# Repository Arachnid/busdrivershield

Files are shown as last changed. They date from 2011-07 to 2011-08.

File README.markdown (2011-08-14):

BusDriver Shield
===============

The BusDriver Shield is a stackable Arduino shield for driving low-power DC or
stepper motors over I2C.

Features:

 - 100% stackable. The number of stacked shields you can drive is limited only
   by the available current on the vin (motor) and 5v rails, and the number of
   I2C addresses available.
 - PWM control for variable speed control.
 - Each board can drive two 1A motors, or the outputs can be combined to drive
   one higher current motor.
 - Optional kickback diodes protect the H-Bridge from inductive kickback.
 - Can be configured to use any valid I2C address in software.
 - Screw terminals for two inputs per motor support a pair of limit switches or
   quadrature encoder per motor. Set-and-forget operation takes the strain of
   handling encoder input off the Arduino.
 - Events can be signalled back to the host board on interrupt pins 2 or 3,
   software-selectable.

Hardware
--------

The BusDriver Shield has two main components: An ATTiny2313 MCU, and an SN754410
quad half H-Bridge. The MCU takes care of the logic and communicates over the
I2C bus, while the H-Bridge takes care of motor driving. Optional kickback
diodes provide additional protection against inductive kickback; also included
are optional power smoothing capacitors and I2C pullups.

Pin assignments for the MCU are as follows:

 - OC1A and OC1B connect to the H-Bridge's enable lines,
   permitting PWM control of each motor.
 - PB0-PB2 and PB6 connect to the input sensors for limit switches or quadrature
   encoders. Pin change interrupts on these lines allow effective handling of
   encoder events.
 - PD2-PD5 connect to the direction control lines on each H-Bridge.
 - PD1 and PD6 connect to Arduino pins 2 and 3 for signalling interrupts to the
   host processor.
 - SCL and SDA connect to the Arduino's A4 and A5 pins for I2C communication
   with the host Arduino.

Software
--------

The ATTiny2313 MCU on each shield exposes an I2C based control interface. All
functionality is exposed via a set of 8-bit registers which can be read and
written over I2C.

To read a register, write a single byte to the device - the register number -
then read a single byte, which will be the contents of the register.

To write a register, write two bytes to the device - the register number and its
value, respectively.

By default, register changes are not persistent, and the device will reset to
its default state if power is removed and restored. Register changes can be 
made permanent by writing to register 255, STORE.

Register mappings are described below.

### Register 0: ADDR

<table>
  <tr><th>7</th><th>6</th><th>5</th><th>4</th><th>3</th><th>2</th><th>1</th><th>0</th></tr>
  <tr><td colspan="8">ADDRESS</td></tr>
</table>

The ADDR register stores the I2C address of the shield as an 8-bit unsigned
integer. Writing to this register will change the shield's address for all future
communications.

### Register 1: STATUS

<table>
  <tr><th>7</th><th>6</th><th>5</th><th>4</th><th>3</th><th>2</th><th>1</th><th>0</th></tr>
  <tr><td colspan="2">Reserved</td><td>INT1</td><td>INT0</td><td>M2_I2</td><td>M2_I1</td><td>M1_I2</td><td>M1_I1</td></tr>
</table>

The STATUS register contains general device status information. The INT0 and
INT1 bits reflect the current status of the two interrupt pins. Writing a 0 to
them will clear the interrupt, while writing a 1 has no effect. The Mx_Iy bits
reflect the current status of input y on motor x. If the relevant
INOPT[x].INVERT_Iy bit is set, the value here will be the inverse of the state
of the actual pin.

### Register 2: DIR

<table>
  <tr><th>7</th><th>6</th><th>5</th><th>4</th><th>3</th><th>2</th><th>1</th><th>0</th></tr>
  <tr><td colspan="4">Reserved</td><td colspan="2">M2</td><td colspan="2">M1</td></tr>
</table>

The DIR register controls the direction of motion for each motor. For each,
values of 00 and 11 indicate no movement - active braking if the motor is
engaged - while 01 and 10 indicate clockwise and counterclockwise motion,
respectively (how this translates into motion on your motor will depend on how
it is wired up).

One special case to note is that if limit switch behaviour is enabled with
INOPT[x].LIMIT_Iy, the limit switch being triggered will set the corresponding
bit of the direction register to 0. If the register was set to 11, this could
cause the motor to start moving. If this behaviour is not desired, set the
register to 00 when no motion is desired.

### Register 3: Reserved

This register is reserved for future use. All reads return 0, and writes will be
ignored.

### Registers 4 & 5: SPEED

<table>
  <tr><th>7</th><th>6</th><th>5</th><th>4</th><th>3</th><th>2</th><th>1</th><th>0</th></tr>
  <tr><td colspan="8">SPEED</td></tr>
</table>

The two speed registers control the speed of each motor. SPEED[0] controls motor
1, while SPEED[1] controls motor 2. Each register is treated as a single 8-bit
unsigned integer. Setting the value to 0 holds the enable pin of the H-Bridge
port for the relevant motor low, while setting it to 255 holds it high.
Intermediate values cause a PWM waveform to be output with a corresponding
duty-cycle.

### Registers 6 & 7: INOPTS

<table>
  <tr><th>7</th><th>6</th><th>5</th><th>4</th><th>3</th><th>2</th><th>1</th><th>0</th></tr>
  <tr><td colspan="2">Reserved</td><td>LIMIT_I2</td><td>LIMIT_I1</td><td>INVERT_I2</td><td>INVERT_I1</td><td>PULLUP_I2</td><td>PULLUP_I1</td></tr>
</table>

The two inopts registers control input options for each motor. INOPTS[0]
controls settings for the first motor, while INOPTS[1] controls settings for the
second one.

LIMIT_I1 and LIMIT_I2 control limit behaviour. If the LIMIT_In bit is set, and
the correspondingly numbered input becomes high (after being inverted, if
specified by INVERT_In), the relevant bit in the direction register will be set
to 0, halting the motor if it was moving. Thus, limit switches can be connected
to the relevant inputs to cause the motor to halt when it reaches a limit. Note
that while the direction bit will be unset, the speed register will be left
unmodified.

INVERT_I1 and INVERT_I2 control how inputs are treated. If the INVERT_In bit is
set, the correspondingly numbered input has its value inverted. This inverted
value is used in all locations, including when considering limit behaviour and
in the STATUS register.

PULLUP_I1 and PULLUP_I2 control the pullups on each input pin. If the relevant
bit is set, pullups will be enabled for that input pin.

### Registers 8 & 9: IMASK

<table>
  <tr><th>7</th><th>6</th><th>5</th><th>4</th><th>3</th><th>2</th><th>1</th><th>0</th></tr>
  <tr><td colspan="4">Reserved</td><td>LIMIT_M2_I2</td><td>LIMIT_M2_I1</td><td>LIMIT_M1_I2</td><td>LIMIT_M1_I1</td></tr>
</table>

The two imask registers control the conditions under which an interrupt will be
triggered. Triggering an interrupt results in setting the relevant bit in the
STATUS register, and pulling the relevant input pin LOW.

When an interrupt is not being triggered, the pin is left in a high-impedance
state. This convention is present for two reasons: By pulling the pin low,
rather than high, pullups can be used by the Arduino to make the pin normally
high. By setting the normal state to high impedance, multiple motor shields can
use the same interrupt line, and if the interrupt is not required, the pin can
be used for other purposes.

Each of the LIMIT_Ma_Ib bits controls whether the input will be triggered when
the corresponding input pin becomes high (after inversion if INOPTS[a].INVERT_Ib
is set).

### Register 127: STORE

Normally, changes made to registers persist only until power is removed. On each
startup, default values for each register are read from the processor's EEPROM.

Writing any value to the STORE register causes the current state of all
registers to be asynchronously written to permanent EEPROM storage. On
subsequent boots, the stored values will be loaded and used as defaults.

Default values, when loaded, are treated the same as if they had been set using
standard I2C commands. As a result, regardless of the value of the STATUS
register when STORE was written to, it will always be initialized with all bits
unset. All other registers, including the speed and direction registers, will
be initialized to the values they had when the write occurred.

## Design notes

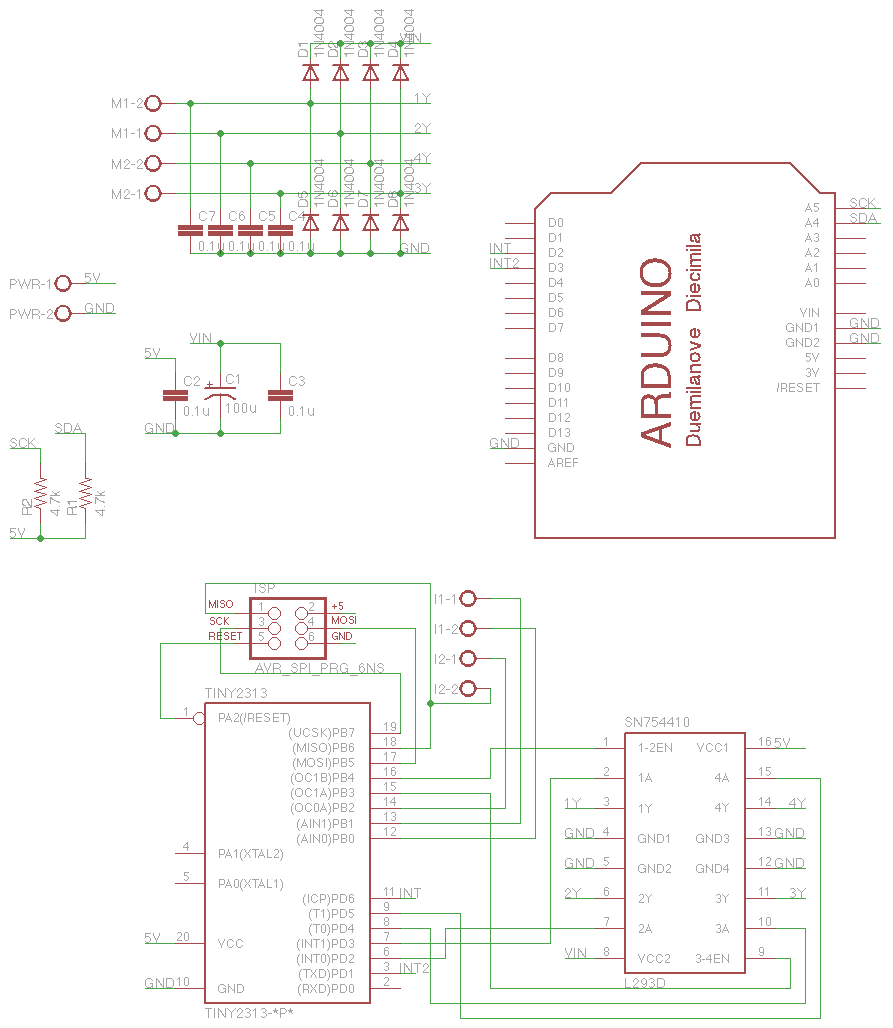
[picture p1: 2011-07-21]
schematics/shield_schematic.png

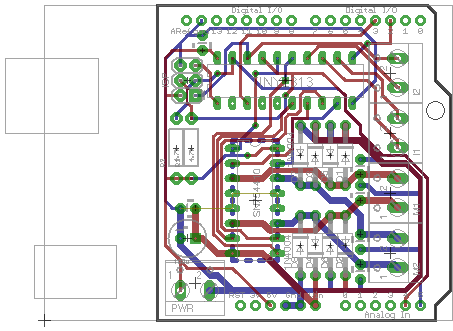
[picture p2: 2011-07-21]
schematics/shield_pcb.png

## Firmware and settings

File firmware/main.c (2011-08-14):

/*
 * BusDriver shield - an I2C based motor driver shield for Arduino.
 * Copyright (C) 2011 Nick Johnson
 *
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
 * You should have received a copy of the GNU General Public License
 * along with this program; if not, write to the Free Software
 * Foundation, Inc., 51 Franklin Street, Fifth Floor, Boston, MA  02110-1301, USA.
 */

#define F_CPU 1000000UL  // 1 MHz

#include <util/delay.h>
#include <avr/io.h>
#include <avr/eeprom.h>
#include <avr/interrupt.h>
#include <avr/pgmspace.h>
#include "register.h"
#include "usiTwiSlave.h"

#define TRUE 1
#define FALSE 0

#define copy_bit(from_reg, from_bit, to_reg, to_bit) if((from_reg) & _BV(from_bit)) { \
    to_reg |= _BV(to_bit); \
} else { \
    to_reg &= ~_BV(to_bit); \
}

#define DDR_ENABLE DDRB
#define DD_ENABLE1 DDB4
#define DD_ENABLE2 DDB3
#define ENABLE_PWM_SETUP() TCCR1A = _BV(WGM10), TCCR1B = _BV(WGM12) | _BV(CS10)
#define TCCR_ENABLE TCCR1A
#define COM_ENABLE1 _BV(COM1B1)
#define COM_ENABLE2 _BV(COM1A1)
#define OCR_ENABLE1 OCR1B
#define OCR_ENABLE2 OCR1A

#define PORT_INPUT PORTB
#define PIN_INPUT PINB
#define P_INPUT_M1_I1 PB6
#define P_INPUT_M1_I2 PB2
#define P_INPUT_M2_I1 PB0
#define P_INPUT_M2_I2 PB1
#define PCINT_MASK _BV(PCINT0) | _BV(PCINT1) | _BV(PCINT2) | _BV(PCINT6)

#define PORT_DIR PORTD
#define P_DIR_M1_CCW PD3
#define P_DIR_M1_CW PD2
#define P_DIR_M2_CCW PD5
#define P_DIR_M2_CW PD4
#define DDR_DIR DDRD
#define DD_DIR1 DDD3
#define DD_DIR2 DDD2
#define DD_DIR3 DDD5
#define DD_DIR4 DDD4

#define PORT_INT PORTD
#define DDR_INT DDRD
#define DD_INT0 DDD6
#define P_INT0 PD6
#define DD_INT1 DDD1
#define P_INT1 PD1

typedef void (*register_write_handler)(uint8_t reg, uint8_t *value);

// Predefinitions of read/write handlers so we can reference them
uint8_t i2c_read(uint8_t reg);
void i2c_write(uint8_t reg, uint8_t value);
void main(void) __attribute__((noreturn));

register_t registers;
// EEPROM copy of registers; updated on write to register 255.
register_t EEMEM eeprom_registers = {
    .reg = {
        .slave_addr = 0x26,
        .status = 0,
        .direction = 0,
        .reserved = 0,
        .speed = {0, 0},
        .inopts = {0, 0},
        .int_mask = {0, 0},
    }
};

volatile uint8_t eeprom_dirty = FALSE;

void write_slave_addr(uint8_t reg, uint8_t *value) {
    usiTwiSlaveInit(*value, i2c_read, i2c_write);
}

void write_status(uint8_t reg, uint8_t *value) {
    // Clear interrupt pins if requested
    if(!(_BV(STATUS_INT0) & *value))
        DDR_INT &= ~_BV(DD_INT0);
    if(!(_BV(STATUS_INT1) & *value))
        DDR_INT &= ~_BV(DD_INT1);
    
    // No writing to input bits, and interrupt bits can only be cleared
    int value_mask = *value | ~(_BV(STATUS_INT0) | _BV(STATUS_INT1));
    *value = value_mask & registers.reg.status;
}

void write_direction(uint8_t reg, uint8_t *value) {
    // Mask out unused bits
    *value &= _BV(DIR_M1_CCW) | _BV(DIR_M1_CW) |
              _BV(DIR_M2_CCW) | _BV(DIR_M2_CW);

    // Unset any bits prohibited by limit switches
    if((registers.reg.status | _BV(STATUS_M1_I1)) &&
       (registers.reg.inopts[0] | _BV(INOPT_LIMIT_I1)))
        *value &= ~_BV(DIR_M1_CCW);
    if((registers.reg.status | _BV(STATUS_M1_I2)) &&
       (registers.reg.inopts[0] | _BV(INOPT_LIMIT_I2)))
        *value &= ~_BV(DIR_M1_CW);
    if((registers.reg.status | _BV(STATUS_M2_I1)) &&
       (registers.reg.inopts[1] | _BV(INOPT_LIMIT_I1)))
        *value &= ~_BV(DIR_M2_CCW);
    if((registers.reg.status | _BV(STATUS_M2_I2)) &&
       (registers.reg.inopts[1] | _BV(INOPT_LIMIT_I2)))
        *value &= ~_BV(DIR_M2_CW);
    
    // Set outputs as required
    copy_bit(*value, DIR_M1_CCW, PORT_DIR, P_DIR_M1_CCW);
    copy_bit(*value, DIR_M1_CW, PORT_DIR, P_DIR_M1_CW);
    copy_bit(*value, DIR_M2_CCW, PORT_DIR, P_DIR_M2_CCW);
    copy_bit(*value, DIR_M2_CW, PORT_DIR, P_DIR_M2_CW);
}

void write_reserved(uint8_t reg, uint8_t *value) {
    //*value = 0;
}

void write_speed(uint8_t reg, uint8_t *value) {
    uint8_t tccr; // TCCR register bitmask to activate the specified motor
    volatile uint16_t *ocr; // Register to set PWM duty cycle for specified motor

    if((reg & 1) == 0) {
        // Motor 1
        tccr = COM_ENABLE1;
        ocr = &OCR_ENABLE1;
    } else {
        // Motor 2
        tccr = COM_ENABLE2;
        ocr = &OCR_ENABLE2;
    }

    if(*value == 0) {
        // Disable PWM for constant 0
        TCCR_ENABLE &= ~tccr;
    } else {
        // Enable PWM and set duty cycle
        TCCR_ENABLE |= tccr;
        *ocr = *value;
    }
}

void write_inopts(uint8_t reg, uint8_t *value) {
    if(reg & 1) {
        copy_bit(*value, INOPT_PULLUP_I1, PORT_INPUT, P_INPUT_M2_I1);
        copy_bit(*value, INOPT_PULLUP_I2, PORT_INPUT, P_INPUT_M2_I2);
    } else {
        copy_bit(*value, INOPT_PULLUP_I1, PORT_INPUT, P_INPUT_M1_I1);
        copy_bit(*value, INOPT_PULLUP_I2, PORT_INPUT, P_INPUT_M1_I2);
    }
    
    // Update input pin status, limits etc
    update_inputs();
}

void write_int_mask(uint8_t reg, uint8_t *value) {
}

const register_write_handler write_handlers[] = {
    write_slave_addr,
    write_status,
    write_direction,
    write_reserved,
    write_speed,
    write_speed,
    write_inopts,
    write_inopts,
    write_int_mask,
    write_int_mask,
};

uint8_t i2c_read(uint8_t reg) {
    if(reg < NUM_REGISTERS) {
        return registers.bytes[reg];
    } else {
        return 0;
    }
}

void i2c_write(uint8_t reg, uint8_t value) {
    if(reg < NUM_REGISTERS) {
        write_handlers[reg](reg, &value);
        registers.bytes[reg] = value;
    } else if(reg == 127) {
        // Update eeprom (asynchronously, so we don't block the interrupt).
        eeprom_dirty = TRUE;
    } else {
        // Invalid register - do nothing.
    }
}

void update_input_pin(uint8_t pin, uint8_t input_id) {
    // This function makes the following assumptions:
    // 1) There are exactly 4 inputs
    // 2) The bit position for each input is the same in the STATUS and IMASK registers
    // 3) Bit 1 of input_id can be used to choose which inopts register to select
    // 4) Bit 0 of input_id can be used to choose which offset into the inopts
    //    register to use for the invert and limit bits.
    // 5) The bit position for each input matches the bit in the direction register
    //    it should clear if limit behaviour is configured.
    
    // Get the contents of the inopts register for this input (assumption 3)
    uint8_t inopts = registers.reg.inopts[input_id >> 1];

    // Get the pin value
    uint8_t val = PIN_INPUT & _BV(pin);

    // If the invert flag is set, invert the input (assumption 4)
    if(inopts & _BV(INOPT_INVERT_I1 + (input_id & 1))) {
        val = !val;
    }
    
    // Update the status register (assumption 2)
    if(val) {
        registers.reg.status |= _BV(input_id);
    } else {
        registers.reg.status &= ~_BV(input_id);
    }
    
    // Stop the motor if limits are set (assumptions 4 & 5)
    if(val && (inopts & _BV(INOPT_LIMIT_I1 + (input_id & 1)))) {
        if(registers.reg.direction & _BV(input_id)) {
            registers.reg.direction &= ~_BV(input_id);
            write_direction(2, &registers.reg.direction);
        }
    }
    
    // Signal an interrupt if requested
    if(registers.reg.int_mask[0] & _BV(input_id)) {
        registers.reg.status |= _BV(STATUS_INT0);
        DDR_INT |= _BV(DD_INT0);
    }
    if(registers.reg.int_mask[1] & _BV(input_id)) {
        registers.reg.status |= _BV(STATUS_INT1);
        DDR_INT |= _BV(DD_INT1);
    }
}

void update_inputs() {
    update_input_pin(P_INPUT_M1_I1, 0);
    update_input_pin(P_INPUT_M1_I2, 1);
    update_input_pin(P_INPUT_M2_I1, 2);
    update_input_pin(P_INPUT_M2_I2, 3);
}   

ISR(PCINT_vect) {
    // One of the input pins has changed value.
    update_inputs();
}

void ioinit(void) {
    // Set the enable pins as outputs
    DDR_ENABLE |= _BV(DD_ENABLE1) | _BV(DD_ENABLE2);
    // Setup PWM: Fast PWM mode, 8-bit, no prescaling. Don't enable it yet.
    ENABLE_PWM_SETUP();
    // Set the direction pins as outputs
    DDR_DIR |= _BV(DD_DIR1) | _BV(DD_DIR2) | _BV(DD_DIR3) | _BV(DD_DIR4);
}

void configure_interrupts(void) {
    // Enable the pin change interrupt for the relevant pins
    PCMSK |= PCINT_MASK;
    // Turn on the pin change interrupt globally
    GIMSK |= _BV(PCIE);
}

void read_registers(void) {
    // Initialize from eeprom
    eeprom_read_block(&registers, &eeprom_registers, sizeof(registers));

    // Run all the write funcs in order to initialize the device
    for(int i = 0; i < NUM_REGISTERS; i++)
        write_handlers[i](i, &registers.bytes[i]);
}

void main(void) {
    ioinit();
    configure_interrupts();
    read_registers();
    // Enable interrupts
    sei();
    
    for(;;) {
        if(eeprom_dirty) {
            eeprom_write_block(&registers, &eeprom_registers, sizeof(registers));
            eeprom_dirty = FALSE;
        }
    }
}

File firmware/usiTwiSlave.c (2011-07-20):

/********************************************************************************

USI TWI Slave driver.

Created by Donald R. Blake. donblake at worldnet.att.net
Adapted by Jochen Toppe, jochen.toppe at jtoee.com
Adapted by Ben Galvin, bgalvin at fastmail.fm

---------------------------------------------------------------------------------

Created from Atmel source files for Application Note AVR312: Using the USI Module
as an I2C slave.

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
---------------------------------------------------------------------------------

Change Activity:

    Date       Description
   ------      -------------
  16 Mar 2007  Created.
  27 Mar 2007  Added support for ATtiny261, 461 and 861.
  26 Apr 2007  Fixed ACK of slave address on a read.
  04 Jul 2007  Fixed USISIF in ATtiny45 def
  12 Dev 2009  Added callback functions for data requests
  12 Apr 2011  Added read/write register callbacks
********************************************************************************/



/********************************************************************************

                                    includes

********************************************************************************/

#include <avr/io.h>
#include <avr/interrupt.h>
#include <stdbool.h>
#include "usiTwiSlave.h"



/********************************************************************************

                            device dependent defines

********************************************************************************/

#if defined( __AVR_ATtiny2313__ )
#  define DDR_USI             DDRB
#  define PORT_USI            PORTB
#  define PIN_USI             PINB
#  define PORT_USI_SDA        PB5
#  define PORT_USI_SCL        PB7
#  define PIN_USI_SDA         PINB5
#  define PIN_USI_SCL         PINB7
#  define USI_START_COND_INT  USISIF
#  define USI_START_VECTOR    USI_START_vect
#  define USI_OVERFLOW_VECTOR USI_OVERFLOW_vect
#endif

#if defined( __AVR_ATtiny25__ ) | \
     defined( __AVR_ATtiny45__ ) | \
     defined( __AVR_ATtiny85__ )
#  define DDR_USI             DDRB
#  define PORT_USI            PORTB
#  define PIN_USI             PINB
#  define PORT_USI_SDA        PB0
#  define PORT_USI_SCL        PB2
#  define PIN_USI_SDA         PINB0
#  define PIN_USI_SCL         PINB2
#  define USI_START_COND_INT  USISIF
#  define USI_START_VECTOR    USI_START_vect
#  define USI_OVERFLOW_VECTOR USI_OVF_vect
#endif

#if defined( __AVR_ATtiny26__ )
#  define DDR_USI             DDRB
#  define PORT_USI            PORTB
#  define PIN_USI             PINB
#  define PORT_USI_SDA        PB0
#  define PORT_USI_SCL        PB2
#  define PIN_USI_SDA         PINB0
#  define PIN_USI_SCL         PINB2
#  define USI_START_COND_INT  USISIF
#  define USI_START_VECTOR    USI_STRT_vect
#  define USI_OVERFLOW_VECTOR USI_OVF_vect
#endif

#if defined( __AVR_ATtiny261__ ) | \
     defined( __AVR_ATtiny461__ ) | \
     defined( __AVR_ATtiny861__ )
#  define DDR_USI             DDRB
#  define PORT_USI            PORTB
#  define PIN_USI             PINB
#  define PORT_USI_SDA        PB0
#  define PORT_USI_SCL        PB2
#  define PIN_USI_SDA         PINB0
#  define PIN_USI_SCL         PINB2
#  define USI_START_COND_INT  USISIF
#  define USI_START_VECTOR    USI_START_vect
#  define USI_OVERFLOW_VECTOR USI_OVF_vect
#endif

#if defined( __AVR_ATmega165__ ) | \
     defined( __AVR_ATmega325__ ) | \
     defined( __AVR_ATmega3250__ ) | \
     defined( __AVR_ATmega645__ ) | \
     defined( __AVR_ATmega6450__ ) | \
     defined( __AVR_ATmega329__ ) | \
     defined( __AVR_ATmega3290__ )
#  define DDR_USI             DDRE
#  define PORT_USI            PORTE
#  define PIN_USI             PINE
#  define PORT_USI_SDA        PE5
#  define PORT_USI_SCL        PE4
#  define PIN_USI_SDA         PINE5
#  define PIN_USI_SCL         PINE4
#  define USI_START_COND_INT  USISIF
#  define USI_START_VECTOR    USI_START_vect
#  define USI_OVERFLOW_VECTOR USI_OVERFLOW_vect
#endif

#if defined( __AVR_ATmega169__ )
#  define DDR_USI             DDRE
#  define PORT_USI            PORTE
#  define PIN_USI             PINE
#  define PORT_USI_SDA        PE5
#  define PORT_USI_SCL        PE4
#  define PIN_USI_SDA         PINE5
#  define PIN_USI_SCL         PINE4
#  define USI_START_COND_INT  USISIF
#  define USI_START_VECTOR    USI_START_vect
#  define USI_OVERFLOW_VECTOR USI_OVERFLOW_vect
#endif

#define NO_CURRENT_REGISTER_SET 255

/********************************************************************************

                        functions implemented as macros

********************************************************************************/

#define SET_USI_TO_SEND_ACK( ) \
{ \
  /* prepare ACK */ \
  USIDR = 0; \
  /* set SDA as output */ \
  DDR_USI |= ( 1 << PORT_USI_SDA ); \
  /* clear all interrupt flags, except Start Cond */ \
  USISR = \
       ( 0 << USI_START_COND_INT ) | \
       ( 1 << USIOIF ) | ( 1 << USIPF ) | \
       ( 1 << USIDC )| \
       /* set USI counter to shift 1 bit */ \
       ( 0x0E << USICNT0 ); \
}

#define SET_USI_TO_READ_ACK( ) \
{ \
  /* set SDA as input */ \
  DDR_USI &= ~( 1 << PORT_USI_SDA ); \
  /* prepare ACK */ \
  USIDR = 0; \
  /* clear all interrupt flags, except Start Cond */ \
  USISR = \
       ( 0 << USI_START_COND_INT ) | \
       ( 1 << USIOIF ) | \
       ( 1 << USIPF ) | \
       ( 1 << USIDC ) | \
       /* set USI counter to shift 1 bit */ \
       ( 0x0E << USICNT0 ); \
}

#define SET_USI_TO_TWI_START_CONDITION_MODE( ) \
{ \
  USICR = \
       /* enable Start Condition Interrupt, disable Overflow Interrupt */ \
       ( 1 << USISIE ) | ( 0 << USIOIE ) | \
       /* set USI in Two-wire mode, no USI Counter overflow hold */ \
       ( 1 << USIWM1 ) | ( 0 << USIWM0 ) | \
       /* Shift Register Clock Source = External, positive edge */ \
       /* 4-Bit Counter Source = external, both edges */ \
       ( 1 << USICS1 ) | ( 0 << USICS0 ) | ( 0 << USICLK ) | \
       /* no toggle clock-port pin */ \
       ( 0 << USITC ); \
  USISR = \
        /* clear all interrupt flags, except Start Cond */ \
        ( 0 << USI_START_COND_INT ) | ( 1 << USIOIF ) | ( 1 << USIPF ) | \
        ( 1 << USIDC ) | ( 0x0 << USICNT0 ); \
}

#define SET_USI_TO_SEND_DATA( ) \
{ \
  /* set SDA as output */ \
  DDR_USI |=  ( 1 << PORT_USI_SDA ); \
  /* clear all interrupt flags, except Start Cond */ \
  USISR    =  \
       ( 0 << USI_START_COND_INT ) | ( 1 << USIOIF ) | ( 1 << USIPF ) | \
       ( 1 << USIDC) | \
       /* set USI to shift out 8 bits */ \
       ( 0x0 << USICNT0 ); \
}

#define SET_USI_TO_READ_DATA( ) \
{ \
  /* set SDA as input */ \
  DDR_USI &= ~( 1 << PORT_USI_SDA ); \
  /* clear all interrupt flags, except Start Cond */ \
  USISR    = \
       ( 0 << USI_START_COND_INT ) | ( 1 << USIOIF ) | \
       ( 1 << USIPF ) | ( 1 << USIDC ) | \
       /* set USI to shift out 8 bits */ \
       ( 0x0 << USICNT0 ); \
}
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

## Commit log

2011-07-19 Added schematic and PCB images
2011-07-20 Added I2C slave library
2011-07-20 Improved decoupling capacitor setup
    [shield.brd, shield.sch]
2011-07-20 Rewired again to move filter cap closer to the MCU
    [shield.brd]
2011-07-21 Reworked again to add caps between motor lines and ground, instead of across motor lines
    [shield.brd, shield.sch]
2011-07-21 Updated PCB and schematic images
2011-07-21 Updated gerber files
    [shield.brd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]
2011-07-21 Minor changes to board layout
2011-07-22 Updated shield to use 3.5mm screw terminals instead of 5mm ones.
    [shield.brd, shield.sch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]
2011-07-24 First revision of firmware. Working, but with no interrupts limits, or input registers
2011-07-24 Minor revisions to schematics
    [shield.brd]
2011-07-26 Replaced bit-setting function with copy_bit macro
    [main.c]
2011-07-28 Fixed a bug in the copy_bit macro
    [main.c]
2011-07-30 Added support for input handling (read, limit, interrupts) - untested
2011-08-09 Changed interrupt behaviour to set pin low when asserted, high-impedance when not
2011-08-11 Revert accidentally commited changes to main.c
    [main.c]
2011-08-13 Fixed bug with PWM enable/disable
    [main.c]
2011-08-13 Fixed some bugs and pin mapping errors
    [main.c]
2011-08-14 Updated direction write routine to respect limit switches, and inopt write routine to update inputs

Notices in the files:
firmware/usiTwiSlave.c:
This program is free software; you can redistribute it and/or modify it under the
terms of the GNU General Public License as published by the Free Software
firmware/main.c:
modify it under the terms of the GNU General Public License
